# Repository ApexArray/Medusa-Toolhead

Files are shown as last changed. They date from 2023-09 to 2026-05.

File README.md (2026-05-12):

# Medusa-Toolhead (Apex Mod)

This project adds several features to [Ch4rlesB's Medusa Toolhead](https://github.com/Ch4rlesB/Medusa-Toolhead/tree/main).

- **New clip-in belt mount design** which eventually became its own project under [Apex Clips](https://github.com/ApexArray/ApexClips)
- **Bottom support brace**
- Added support for ebb36 toolhead board (keeps original support for umbilical and Hartk board)
- Lowered X endstop so that it activates against the Y carriage block (removes need for endstop flag)
- Strengthened zip tie slots
- Added right-side support arm (print with supports in slicer)
- Resized heat insert slots from 3.9D -> 3.8D

https://github.com/ApexArray/Medusa-Toolhead/assets/91706106/2dc37877-ce4a-4b54-b629-3e299c2d5c1f

New files are under the ./Apex_Mod folder:
- [STLs](./Apex_Mod/stls/)
- [CAD](./Apex_Mod/CAD/)

All other STLs (not modified by me) can be found in the original [./stls](./stls) directory

## Apex Clips

This solution is designed to be:
- Light-weight
- Strong
- Semi-toolless
- Easy to assemble

Insert the belt into the cavity, and slide in a printable clip to hold it in place.

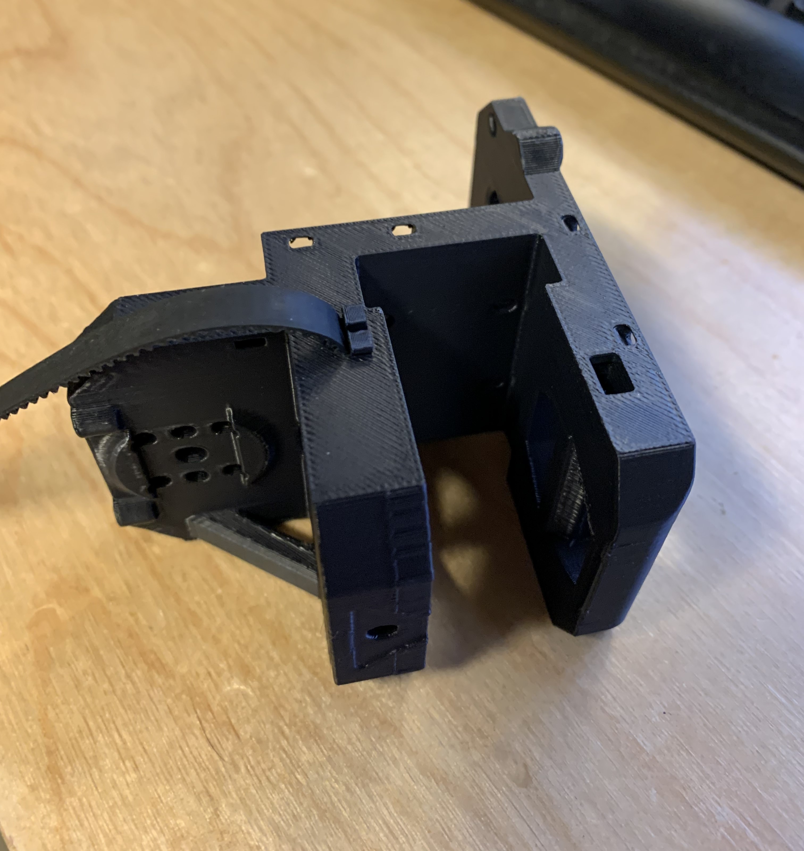
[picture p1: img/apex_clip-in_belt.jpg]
Clip-in belt

Clip-in belt weight

https://github.com/ApexArray/Medusa-Toolhead/assets/91706106/179e2e59-fea6-49be-8833-3ce2743f321f

**Installation tip:** The two front clips sit between the belt and X gantry, and might be difficult to install if you have big fingers. I use a screwdriver or thin wrench to keep the clip aligned while sliding it into the cavity.

## Bottom support block

The original toolhead has excessive Y wobble during fast printing. The fan duct provides some support, but the duct itself is cantilevered from the back and seemed to result in a "diving board" board effect.

The block is attached using two m3x35mm screws and reinforces the front of the toolhead to mitigate any bouncing/wobbling.

While this does seem to be more rigid, I don't have empirical results at the moment as my X rail seems to have developed wobble some time in between testing.

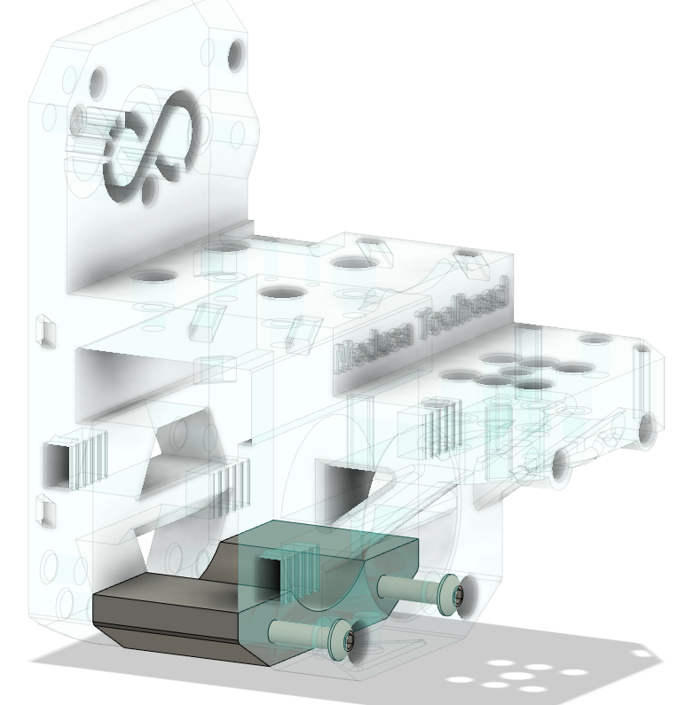
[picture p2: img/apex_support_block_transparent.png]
apex support block transparent

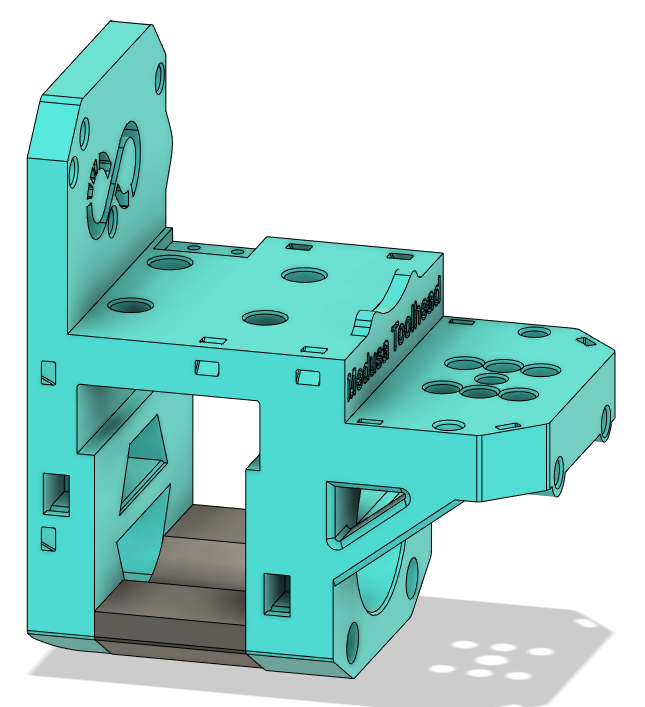
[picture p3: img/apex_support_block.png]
apex support block


## CAD

I tried to keep a tidy f360 timeline on this project. With some exceptions, most features are contained in their own group and labeled accordingly. You should be able to delete/change most features without affecting the rest of the model.

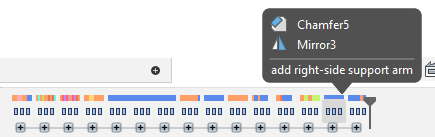
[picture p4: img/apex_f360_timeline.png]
apex f360 timeline


## BOM

Uses the same hardware from the original project, plus:
- 2x m3x35mm screws (bottom support block)
- +2 heat inserts (bottom support block)
- +2 heat inserts (for ebb36 + hartk/umbilical support)

## TODO

- Further input shaper testing (with and without bottom support block)
- Reinforce as needed to strengthen Y movement (potentially reinforce further using longer m3x40mm screws for the hotend fan)
- Additional probe options (e.g., BLTouch, Cargogropher), as the current klicky implementation has a very large Y offset and cannot probe the front portion of the bed.

## LICENSE
All files released under the same [GNU General Public License v3.0](./LICENSE) as the original project.

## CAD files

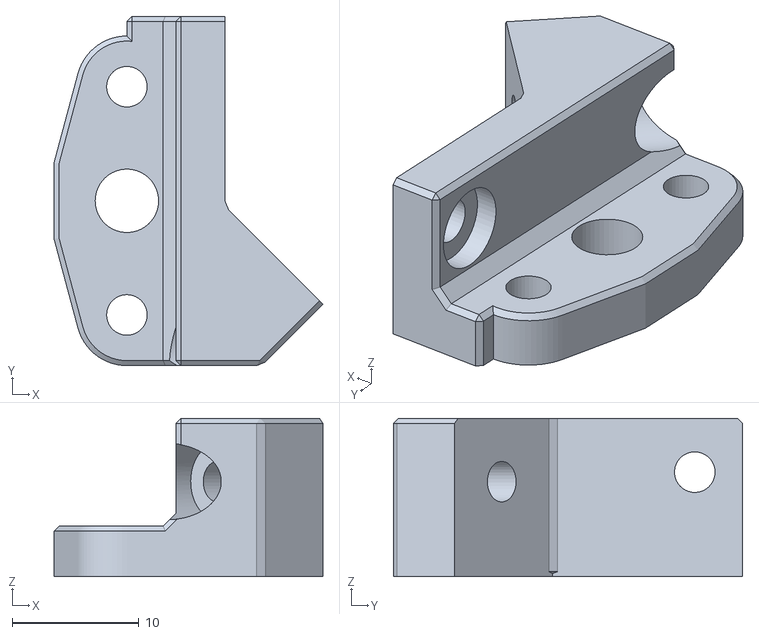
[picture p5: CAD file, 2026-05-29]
Apex_Mod/stls/OPTIONAL_BL-touch-mount_1.stl
21.2 x 27.5 x 12.5

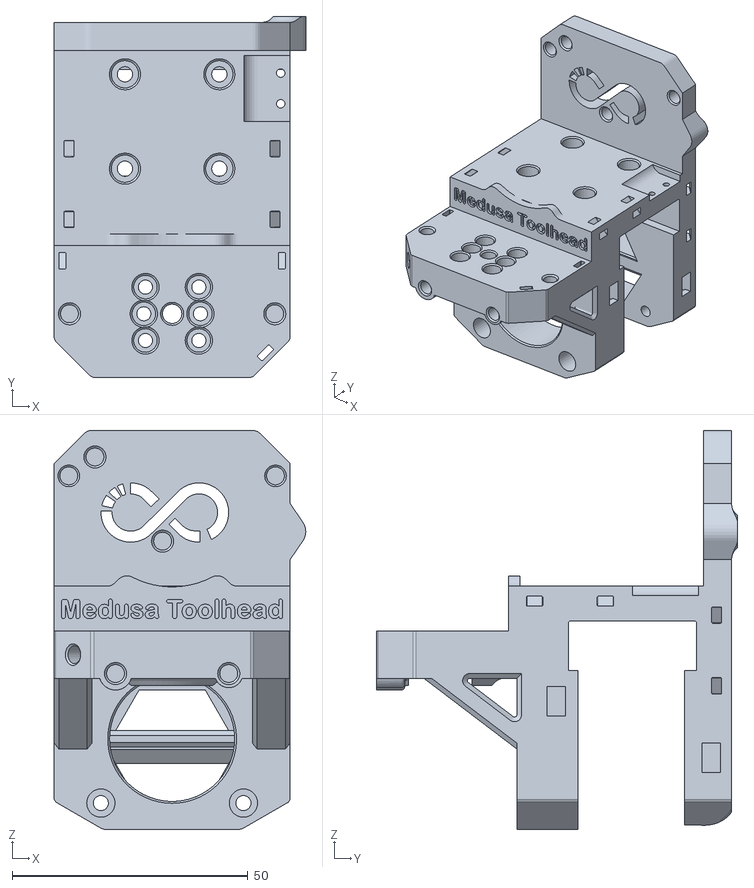
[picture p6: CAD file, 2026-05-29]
Apex_Mod/stls/medusa_2020_body_1.stl
53.3 x 76.5 x 84.6

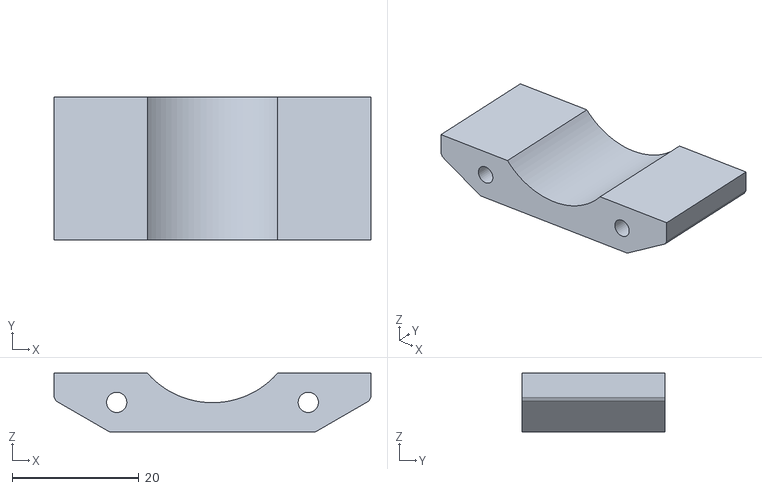
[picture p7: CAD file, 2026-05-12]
Apex_Mod/stls/support_block_1.stl
50.0 x 22.5 x 9.24

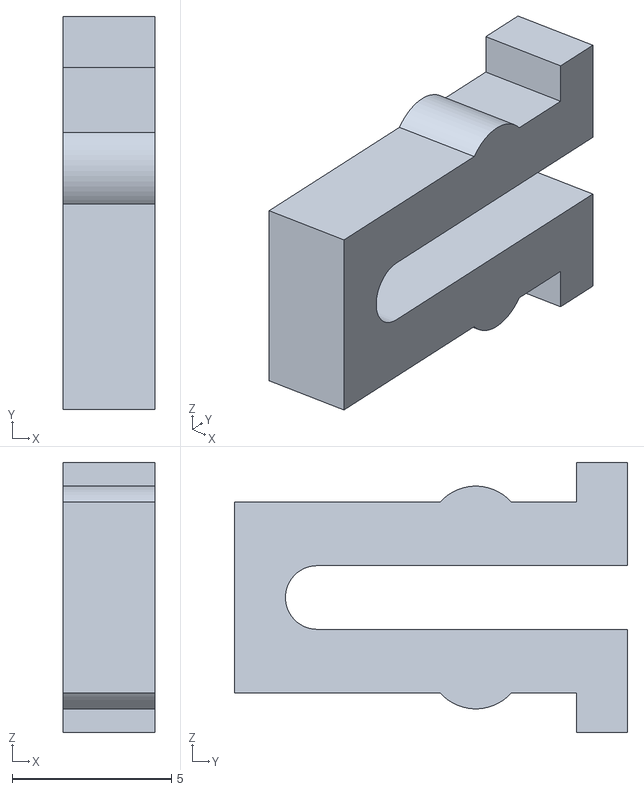
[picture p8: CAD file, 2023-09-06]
Apex_Mod/stls/medusa_belt_clip_4.stl
2.90 x 12.4 x 8.50

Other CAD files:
Apex_Mod/CAD/apex-belt-clip_mk4.f3d
Apex_Mod/CAD/medusa_apex 2020.f3z

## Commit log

2023-09-06 add apex mod files
    [apex-belt-clip_mk4.f3d, medusa_2020_body_1.stl, medusa_belt_clip_4.stl]
2026-05-12 update CAD with reference hotend, fans, and klicky probe
    [medusa_apex 2020.f3z]
2026-05-12 add support block STL
    [support_block_1.stl]
2026-05-29 add bl-touch mount
    [OPTIONAL_BL-touch-mount_1.stl, medusa_2020_body_1.stl]
